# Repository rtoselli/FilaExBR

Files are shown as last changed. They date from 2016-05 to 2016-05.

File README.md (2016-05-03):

# FilaExBR

Código e hardware para uma filamentadora simples de baixo custo, com controle pid para a temperatura e PWM para a velocidade do motor.
O codigo está em constante desenvolvimento, acompanhe o repositório para as últimas versões.

Todo o conteúdo desse repositório está disponivel sob a licença GNU - GPL, e não me responsabilizo por qualquer dano pelo o uso impróprio dos arquivos contidos aqui.

-----

Hardware and code for a simple filament extruder control board with low cost and high power, PID and PWM for motor/temperature control. 
The code evolves fast, keep an eye for new versions. 

All files in this repository are under the GNU - GPL license, use at your own risk, i am not responsible for any harm done by the misuse of the files contained here.

# Board 

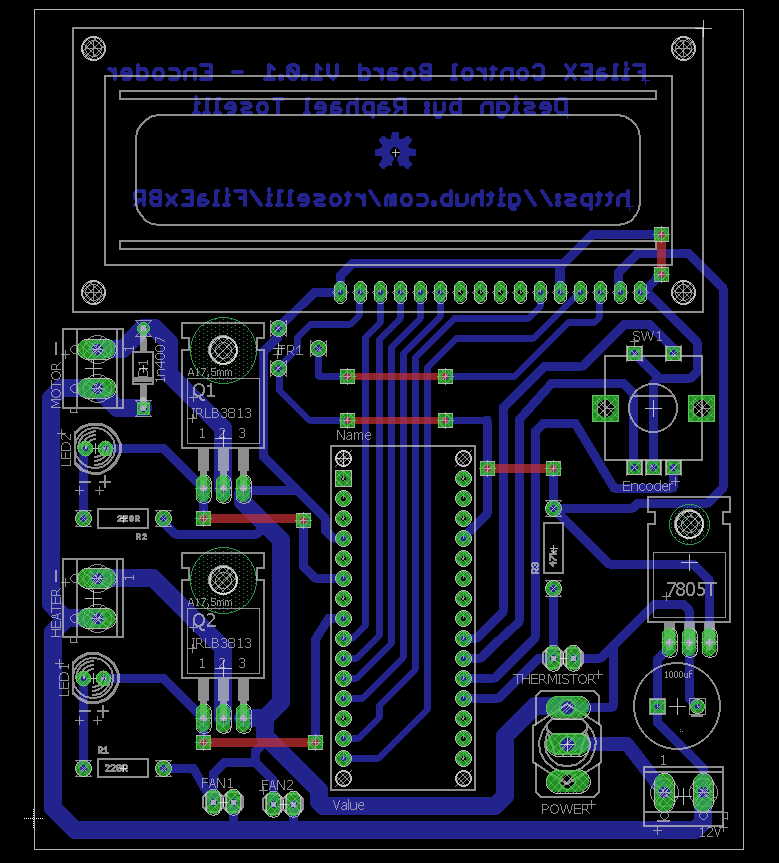
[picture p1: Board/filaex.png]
FilaExBR


The top layer routing represent jumpers, no need for a double sided PCB!
You can see a basic functions video here : https://www.youtube.com/watch?v=0D0GXgb3E8Y

#Bill of materials
Pin Header 1x2 - 3 

Terminal block 5mm - 3

D1 - 1n4007
 
Linear Regulator 7805 - 1 

LED5MM - 2 
                                                        
Switch SPDT - 15A @ 12V - 1 

IRLB3813 N-Channel Enhancement MOSFET (HEXFET); 30V; 100A~ - 2 
                              
R1 - 220R

R2 - 220R

R3 - 47k

Trimpot 300R

ALPS rotary Encoder EC12E with switch - 1
                                                                             
ARDUINO NANO - 1

LCD Display HD44780LCD 16X02 - 1

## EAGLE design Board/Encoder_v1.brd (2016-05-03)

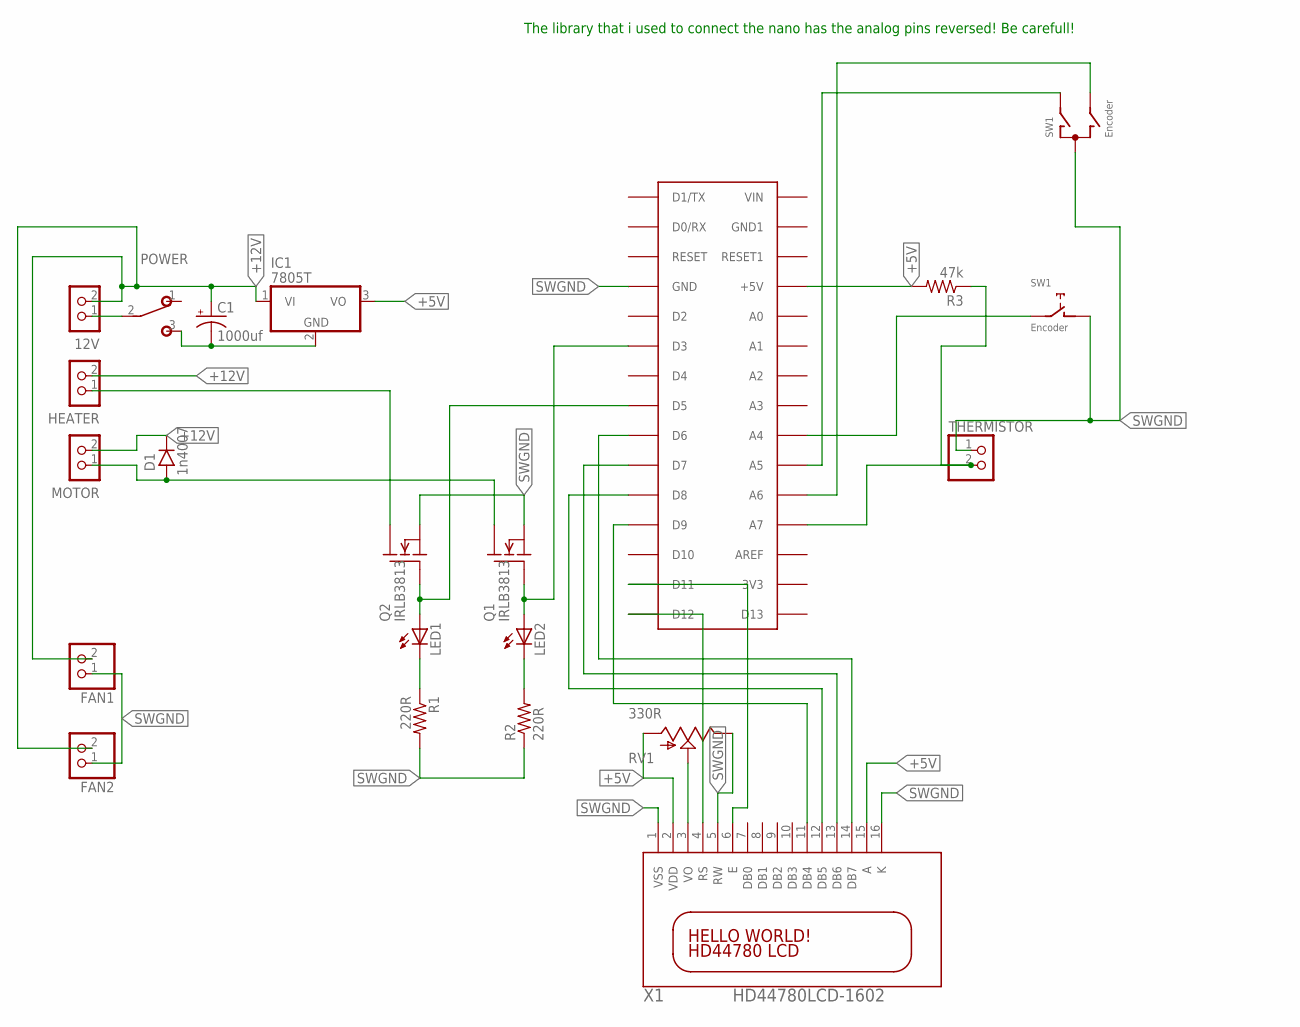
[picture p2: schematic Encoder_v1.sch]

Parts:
12V: CON_TERMINAL_BLOCK_02-5MM; TERMINAL_BLOCK_2P_5
A01: ARDUINO NANO; PDIP-32
C1: 1000uf; CPOL-RADIAL-1000UF-25V
D1: 1n4007; DO41-4
FAN1, FAN2: PINHD-1X2; 1X02
HEATER: CON_TERMINAL_BLOCK_02-5MM; TERMINAL_BLOCK_2P_5
IC1: 7805T; TO220H
LED1, LED2: LED5MM
MOTOR: CON_TERMINAL_BLOCK_02-5MM; TERMINAL_BLOCK_2P_5
POWER: SPDT; M9040P
Q1, Q2: IRLB3813; TO220
R1, R2: 220R; AXIAL-0.4
R3: 47k; AXIAL-0.4
RV1: 330R; TRIM_POT
SW1: Encoder; ALPS_EC12E_SW
THERMISTOR: PINHD-1X2; 1X02
X1: HD44780LCD-1602; LCD1602

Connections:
+5V: A01.+5V, IC1.3 (VO), R3.P$2 (2), RV1.3 (A), X1.2 (VDD), X1.15 (A)
+12V: 12V.2, C1.1 (+), D1.C, FAN1.2, FAN2.2, HEATER.2, IC1.1 (VI), MOTOR.2
unnamed: LED1.K (C), R1.P$1 (1)
unnamed: RV1.1 (S), X1.3 (VO)
unnamed: A01.A4, SW1.E (2)
unnamed: 12V.1, POWER.2
unnamed: A01.A6, SW1.B
unnamed: A01.A7, R3.P$1 (1), THERMISTOR.2
unnamed: A01.A5, SW1.A
unnamed: LED2.K (C), R2.P$2 (2)
unnamed: A01.D5, LED1.A, Q2.1 (G)
unnamed: A01.D6, X1.14 (DB7)
unnamed: A01.D7, X1.13 (DB6)
unnamed: D1.A, MOTOR.1, Q1.2 (D)
unnamed: A01.D3, LED2.A, Q1.1 (G)
unnamed: A01.D8, X1.12 (DB5)
unnamed: A01.D9, X1.11 (DB4)
unnamed: HEATER.1, Q2.2 (D)
unnamed: A01.D11, X1.6 (E)
unnamed: A01.D12, X1.4 (RS)
SWGND: A01.GND, C1.2 (-), FAN1.1, FAN2.1, IC1.2 (GND), POWER.3 (S), Q1.3 (S), Q2.3 (S), R1.P$2 (2), R2.P$1 (1), RV1.2 (E), SW1.C, SW1.D (1), THERMISTOR.1, X1.1 (VSS), X1.5 (RW), X1.16 (K)

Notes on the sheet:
The library that i used to connect the nano has the analog pins reversed! Be carefull!

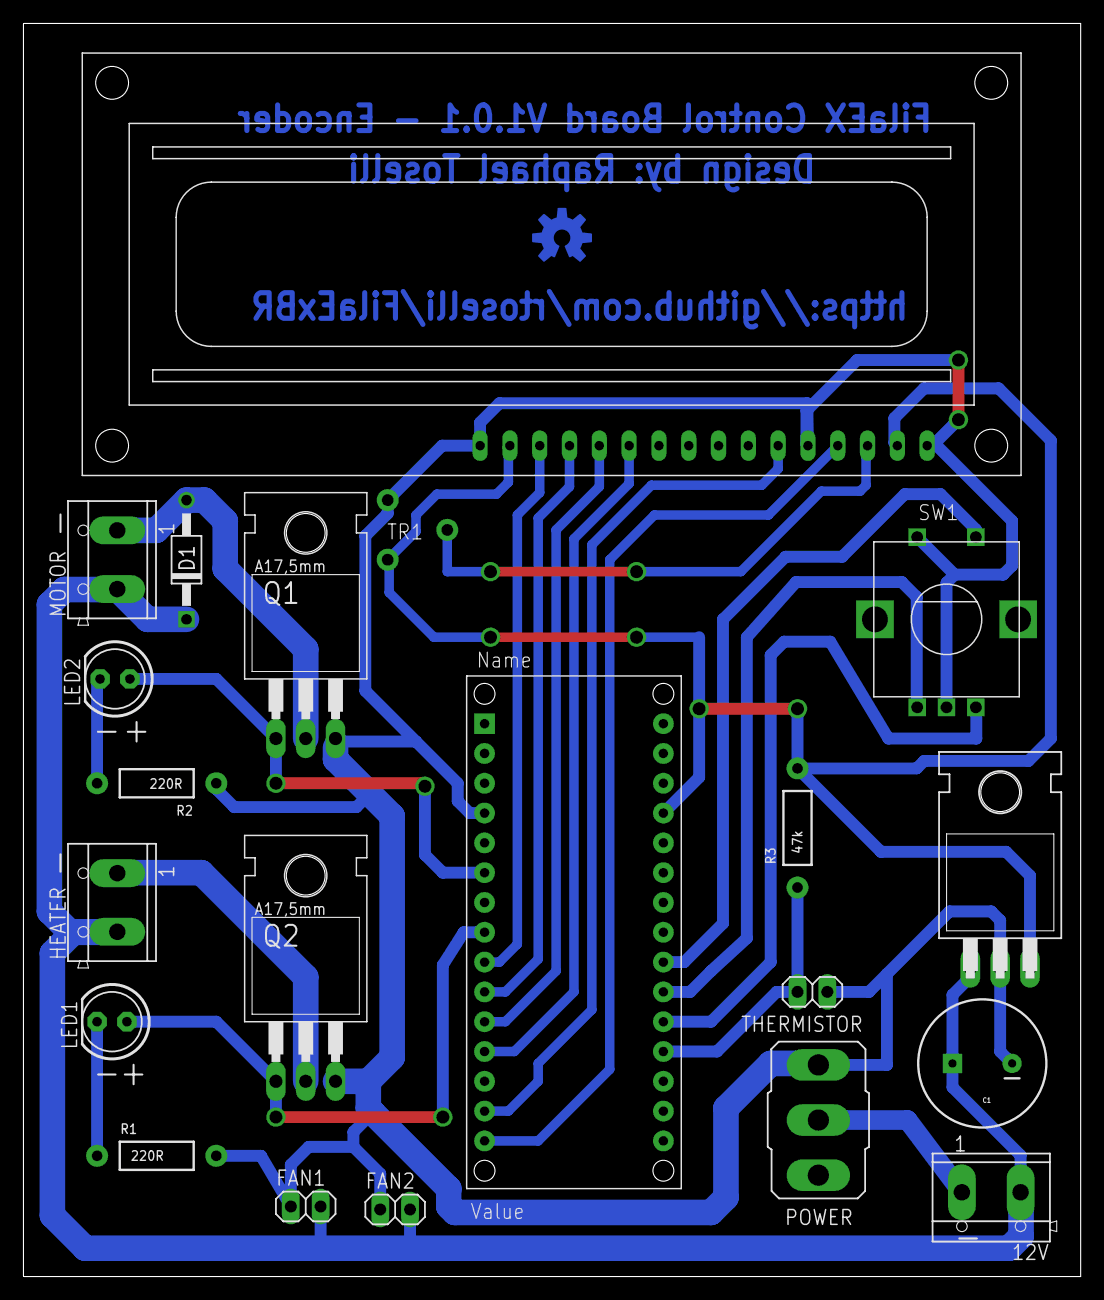
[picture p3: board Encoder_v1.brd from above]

Board: 2 copper layers, 90.1 x 106.8 mm, 22 parts (1 on the bottom side), 21 nets.

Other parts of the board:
U$3: OSHW-LOGO-M_COPPER

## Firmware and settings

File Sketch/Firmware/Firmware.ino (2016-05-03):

/*
  FilaEx FW02

  Raphael Toselli

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
  You should have received a copy of the GNU General Public License
  along with this program.  If not, see <http://www.gnu.org/licenses/>.
*/

// Libraries:
#include <LiquidCrystal.h>
#include <Bounce2.h>
#include <PID_v1.h>
#include <Encoder.h>

//#define DEBUGMODE 1

#define FW_VER "V1.3.6 - Encoder"
#define ABS_TEMP 220
#define PLA_TEMP 180
#define PET_TEMP 220

#define THERMISTOR_PIN A0
#define MOTOR_PIN 3
#define HEATER_PIN 5
#define ENCODER0_SW A3
#define ENCODER0_A A1
#define ENCODER0_B A2

#define TEMP_SAMPLES 10
#define MAX_TEMP 280
#define MIN_TEMP_DIFF_MOTOR 15
#define MIN_EXTRUSION_TEMP 160

#define NUMTEMPS 20
short temptable[NUMTEMPS][2] = {
  {1, 841},
  {54, 255},
  {107, 209},
  {160, 184},
  {213, 166},
  {266, 153},
  {319, 142},
  {372, 132},
  {425, 124},
  {478, 116},
  {531, 108},
  {584, 101},
  {637, 93},
  {690, 86},
  {743, 78},
  {796, 70},
  {849, 61},
  {902, 50},
  {955, 34},
  {1008, 3}
};



// Globals 

int debugTemp = 165;
int incrementRate = 5; 
int tempSet = 0;
int rpmSet = 255;
int actualTemp = 0;
int sample = 0;
int tempArray[TEMP_SAMPLES];
int EncSWLastState = 1;
int animState = 0;
long timertemp = 0;
long btmillis = 500;
long encoder0OldPos  = -999;
bool heaterOn = false;
bool motorOn = false;
bool menuState = false;




// PID
double Input, Output;
double Setpoint;
int NewSetpoint;
//Define the aggressive and conservative Tuning Parameters
double aggKp=4, aggKi=0.2, aggKd=1;
double consKp=1, consKi=0.05, consKd=0.25;
//Timer
int WindowSize = 400;
unsigned long windowStartTime;

//Specify the links and initial tuning parameters
PID heaterPID(&Input, &Output, &Setpoint, consKp, consKi, consKd, DIRECT);

// initialize the library with the numbers of the interface pins
LiquidCrystal lcd(12, 11, 9, 8, 7, 6);

Bounce btEncoder = Bounce();

Encoder E0(ENCODER0_A, ENCODER0_B);

void setup() {
  pinMode(HEATER_PIN, OUTPUT);
  pinMode(MOTOR_PIN, OUTPUT);

  btEncoder.attach(ENCODER0_SW);
  btEncoder.interval(100);

  pinMode(ENCODER0_SW, INPUT);
  digitalWrite(ENCODER0_SW, HIGH);

  pinMode(ENCODER0_A, INPUT);
  digitalWrite(ENCODER0_A, HIGH);

  pinMode(ENCODER0_B, INPUT);
  digitalWrite(ENCODER0_B, HIGH);

  digitalWrite(HEATER_PIN, heaterOn);
  digitalWrite(MOTOR_PIN, motorOn);
  Serial.begin(9600);
  



  // set up the LCD's number of columns and rows:
  lcd.begin(16, 2);
  lcd.setCursor(0, 0);
  // Print a message to the LCD.
  lcd.print("FilaExt");
  lcd.setCursor(0, 1);
  lcd.print(FW_VER);
  delay(1200);
  lcd.clear();
  windowStartTime = millis();
  PIDsetup();

  Serial.print("OK");

}

void loop() {
  
  btEncoder.update();
  
  long newPosition = E0.read();
  if ( newPosition !=  encoder0OldPos ) { 
    
    if ( menuState == false )
    {
      if (newPosition >  encoder0OldPos) 
        temp_up();
      else 
        temp_down();
    }
    else if ( menuState == true ) 
    {
      if ( newPosition >  encoder0OldPos ) 
        rpm_up();
      else 
        rpm_down();
    
    }
  encoder0OldPos = newPosition;
}

  #ifdef DEBUGMODE
    char incomingByte;
    char bufferc[] = {' ',' ',' ',' ',' '};
    if (Serial.available())
    {
        Serial.readBytesUntil('\n', bufferc, 5);
        debugTemp = constrain(atoi(bufferc),0,MAX_TEMP);
    }
  #endif
  
  AquireTempSamples();

  
  if ( menuState == 0 )
    SetTemp();
  else
    RpmControl();

  RunPID();

  if ( motorOn )
    analogWrite(MOTOR_PIN, rpmSet);
  else
    digitalWrite(MOTOR_PIN, LOW);

  int SWState =  btEncoder.read();
  
  if ( SWState == 0 && EncSWLastState != SWState )
  {
    menuState = !menuState;
    EncSWLastState = SWState; 
    
  } else {
    
    EncSWLastState = 1;
  }

    
}

void RunPID()
{
  Setpoint = tempSet;
  Input = actualTemp;
  
  double gap = abs(Setpoint - Input); //distance away from setpoint
  printDebugData("Gap: " + String(gap));
  if (gap < 10)
  { //we're close to setpoint, use conservative tuning parameters
    printDebugData("PID MODE: Conservative");
    heaterPID.SetTunings(consKp, consKi, consKd);
  }
  else
  {
    printDebugData("PID MODE: Aggressive");
    //we're far from setpoint, use aggressive tuning parameters
    heaterPID.SetTunings(aggKp, aggKi, aggKd);
  }
  
  heaterPID.Compute();
  
  unsigned long now = millis();
  if(now - windowStartTime>WindowSize)
  { //time to shift the Relay Window
    windowStartTime += WindowSize;
  }

  if(Output > now - windowStartTime) 
  {
    digitalWrite(HEATER_PIN,HIGH);
    heaterOn = true ;
  }
  else 
  {
    digitalWrite(HEATER_PIN,LOW);
    heaterOn = false;
  }

}

void RpmControl()
{

  lcd.setCursor(0, 0);
  lcd.print("Motor PWM");
  lcd.print("        ");
  lcd.setCursor(0, 1);
  lcd.print((rpmSet * 100) / 255);
  lcd.print("%                ");

}

void printDebugData(String data)
{
  #ifdef DEBUGMODE
    //Serial.println(data);
    //delay(400);
  #endif
}

void SetTemp()
{



  if ( sample >= TEMP_SAMPLES && abs(millis() - timertemp) > 100)
  {
    lcd.setCursor(0, 0);
    actualTemp = getTemp();
    String tempStr = String("Temp ");
    tempStr += actualTemp ;
    tempStr += "/" +  String(tempSet);
    //module.clearDisplay();
    lcd.print(tempStr);
    lcd.print("        ");
    lcd.setCursor(0, 1);
    char c = animate();
    lcd.print("Heat:");
    lcd.print(( heaterOn ? c : '-'));
    lcd.print(" Mot:");
    lcd.print(( motorOn ? c : '-'));
    lcd.print("        ");
    if ( abs(tempSet - actualTemp) > MIN_TEMP_DIFF_MOTOR || actualTemp < MIN_EXTRUSION_TEMP ) {
      motorOn = false;
    }
    else if ( ( abs(tempSet - actualTemp)  <= MIN_TEMP_DIFF_MOTOR && actualTemp >= MIN_EXTRUSION_TEMP ))
    {
      motorOn = true;
    }
    sample = 0;
    timertemp = millis();
  }

}


void AquireTempSamples()
{

  if (sample < TEMP_SAMPLES )
  {
    tempArray[sample] = read_temp();
    sample++;
  }

}


char animate()
{
  char c;
  switch(animState)
  {
    case 0:
          c = '|';
          break;
    case 1:
          c = '/';
          break;
    case 2:
          c = '-';
          break;
    case 3:
          c = 92;
          animState = -1;
          break;
          
  }
  animState++;
  return c;
  
}
int getTemp()
{
  int auxTemp = 0;
  for ( int i = 0; i < TEMP_SAMPLES; i++)
  {
    //Serial.println(tempArray[i]);
    auxTemp += tempArray[i];
  }

  /*Serial.print("T:");
    Serial.println(auxTemp / TEMP_SAMPLES);*/

#ifdef DEBUGMODE
  return debugTemp;
#else
  return auxTemp / TEMP_SAMPLES;
#endif

}
void temp_up()
{

  if ( millis() -  btmillis > incrementRate && tempSet < MAX_TEMP )
  {
    tempSet += 1;
    btmillis = millis();
  }
}

void temp_down()
{
  if (  millis() - btmillis > incrementRate && tempSet > 0 )
  {
    tempSet -= 1;
    btmillis = millis();
  }
}


void rpm_down()
{
  if (  millis() - btmillis > incrementRate && rpmSet > 0 )
  {
    rpmSet -= 5;
    btmillis = millis();
  }
}


void rpm_up()
{

  if ( millis() -  btmillis > incrementRate && rpmSet < 255 )
  {
    rpmSet += 5;
    btmillis = millis();
  }
}


int read_temp()
{
  int rawtemp = analogRead(THERMISTOR_PIN);
  int current_celsius = 0;

  byte i;
  for (i = 1; i < NUMTEMPS; i++)
  {
    if (temptable[i][0] > rawtemp)
    {
      int realtemp  = temptable[i - 1][1] + (rawtemp - temptable[i - 1][0]) * (temptable[i][1] - temptable[i - 1][1]) / (temptable[i][0] - temptable[i - 1][0]);

      if (realtemp > 255)
        realtemp = 255;

      current_celsius = realtemp;

      break;
    }
  }

  // Overflow: We just clamp to 0 degrees celsius
  if (i == NUMTEMPS)
    current_celsius = 0;

  return current_celsius;
}

void PIDsetup() {
  lcd.setCursor(0, 0);
  lcd.print("  Configurando ");
  lcd.setCursor(0, 1);
  lcd.print("     P I D    ");
  delay(1000);
  //analogReference(EXTERNAL);
  for (int i = 0; i < TEMP_SAMPLES; i++)
    AquireTempSamples();

  //Timer
  windowStartTime = millis();

  heaterPID.SetOutputLimits(0, WindowSize);//tell the PID to range between 0 and the full window size
  //inizializzo le variabili
  Input = getTemp();
  printDebugData("Temp: " + String(Input));
  heaterPID.SetMode(AUTOMATIC);
}

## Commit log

2016-04-16 Ajuste de parametros do PID, Funçoes de debug e ajuste do nome do sketch
2016-04-16 Parametros PID modificados
2016-04-18 Adição dos arquivos de layout da PCB
    [Encoder_v1.brd, Encoder_v1.sch]
2016-04-29 Minor Updates na placa, update do código, inicio da programação do encoder
    [Encoder_v1.brd, Encoder_v1.sch]
2016-04-29 Controle de menu por encoder
2016-05-03 Update board files and readme
    [Encoder_v1.brd, Encoder_v1.sch]
2016-05-03 Pin adjustment on the firmware

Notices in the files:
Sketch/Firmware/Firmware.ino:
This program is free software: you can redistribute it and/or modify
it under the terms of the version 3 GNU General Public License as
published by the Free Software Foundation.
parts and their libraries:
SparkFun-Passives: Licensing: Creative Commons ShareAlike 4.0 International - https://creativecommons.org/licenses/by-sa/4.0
